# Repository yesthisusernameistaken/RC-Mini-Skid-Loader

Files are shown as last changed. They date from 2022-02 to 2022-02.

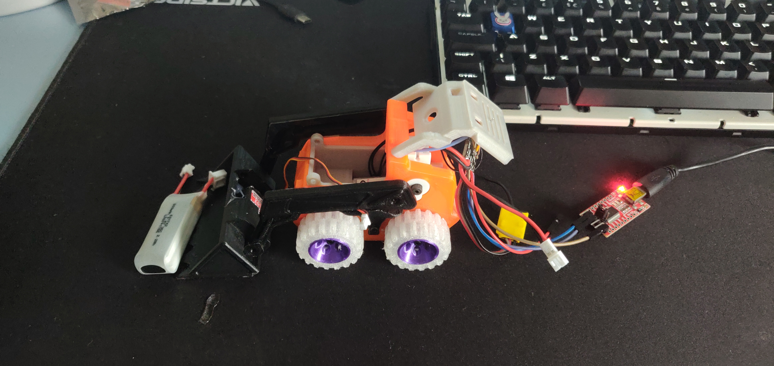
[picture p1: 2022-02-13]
2022-02-13 11.58.56.jpg

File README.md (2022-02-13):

<div align="center">
<h1> RC-Mini-Skid-Loader
</div>

Idea from here: https://blog.naver.com/3dfuns/221406762117
Modified version to use N20 Motors: https://www.thingiverse.com/thing:4548756

Wheels printed in TPU instead of buying Lego versions.

The code on the Tinydrive was not working for some unknown reason. Possibly compatibility issues with the PPM receiver used.
Wrote custom code. Based on code previously used for a project but modified to use the pins and hardware on the Tinydrive.  
Running into an issue where the Servo library disables the pins used for controlling one of the motors. Also might be running out of timers. 

<p align="center">


  ## Shopping List </div>
| Part | Price (€) | Link |
|---|:---:|---|
| TinyDrive | 25 | https://store.flytron.com/collections/electronic-parts/products/tiny-drive-v1-sbus-ppm-1-5a-dual-motor-controller |
| FS-RX2A Pro Receiver | 10 | https://www.aliexpress.com/item/32845028381.html |
| AFRC D1602 Nano 2.2g Mricro Servo | 8 | https://www.banggood.com/AFRC-D1602-Nano-2_2g-Mricro-Servo-Coreless-Digital-Servo-For-RC-Helicopter-Airplane-Car-p-1684246.html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 |
| Wheels 92402 55982 30.4x14mm | 6 | https://www.aliexpress.com/item/32958796717.html? |
| N20 Motors | 10 | https://www.aliexpress.com/item/33022320164.html |
| Type-C Charging Board TP4056 | 1 | https://www.aliexpress.com/item/32649780468.html? |
| 2S Battery | 10 | |
| Total = | 70 | |

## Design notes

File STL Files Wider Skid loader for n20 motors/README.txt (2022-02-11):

Wider 3DFuns Skid loader for n20 motors by 3DFerret on Thingiverse: https://www.thingiverse.com/thing:4548756

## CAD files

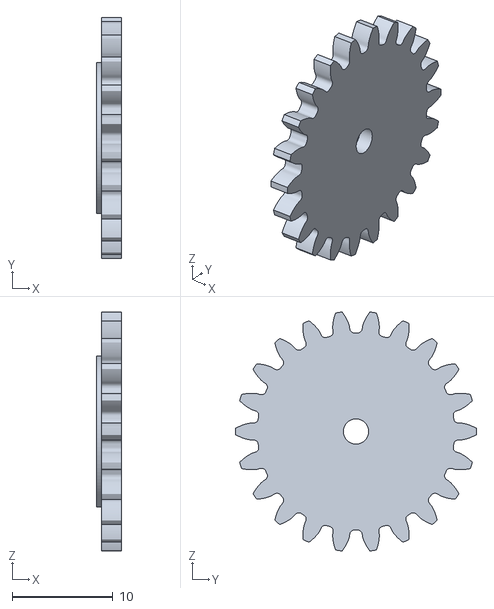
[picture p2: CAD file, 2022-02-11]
STL Files Wider Skid loader for n20 motors/wheel_gear_middle.stl
2.50 x 23.9 x 23.7

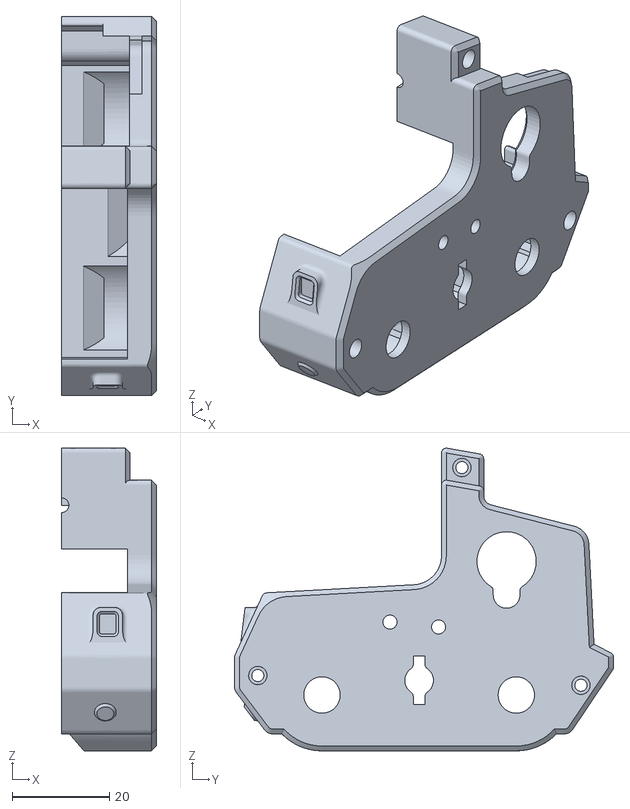
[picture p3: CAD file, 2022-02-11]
STL Files Wider Skid loader for n20 motors/body_right.stl
19.5 x 78.0 x 62.3

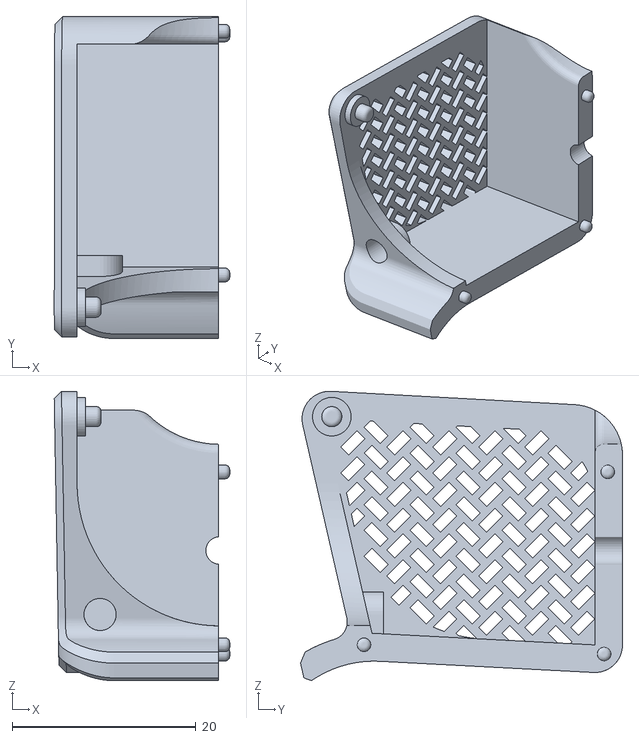
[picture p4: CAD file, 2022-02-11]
STL Files Wider Skid loader for n20 motors/cab_enclosure_right.stl
19.1 x 35.0 x 31.5

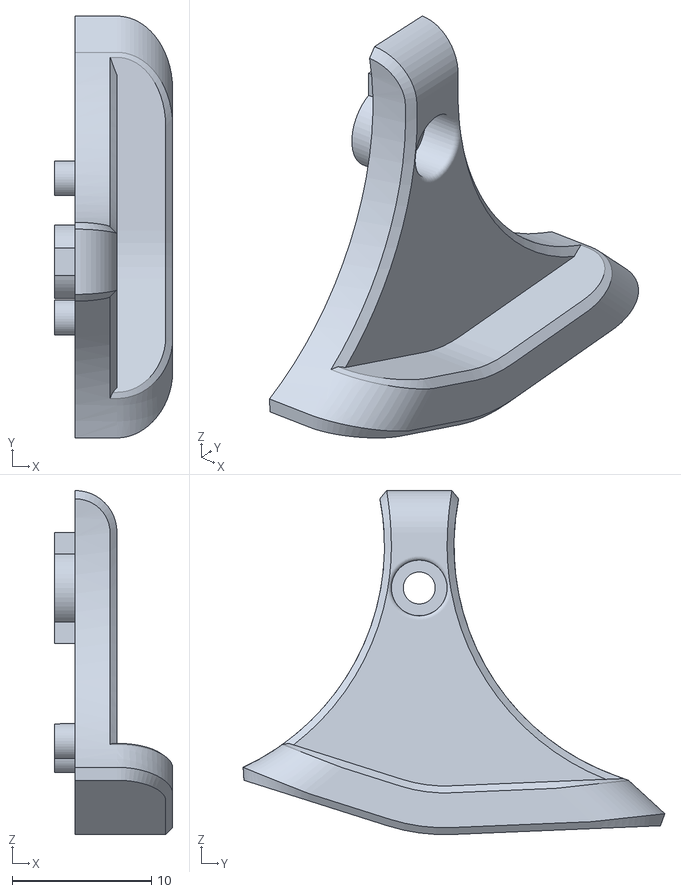
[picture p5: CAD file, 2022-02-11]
STL Files Wider Skid loader for n20 motors/loader_fender_new.stl
8.50 x 30.3 x 24.7

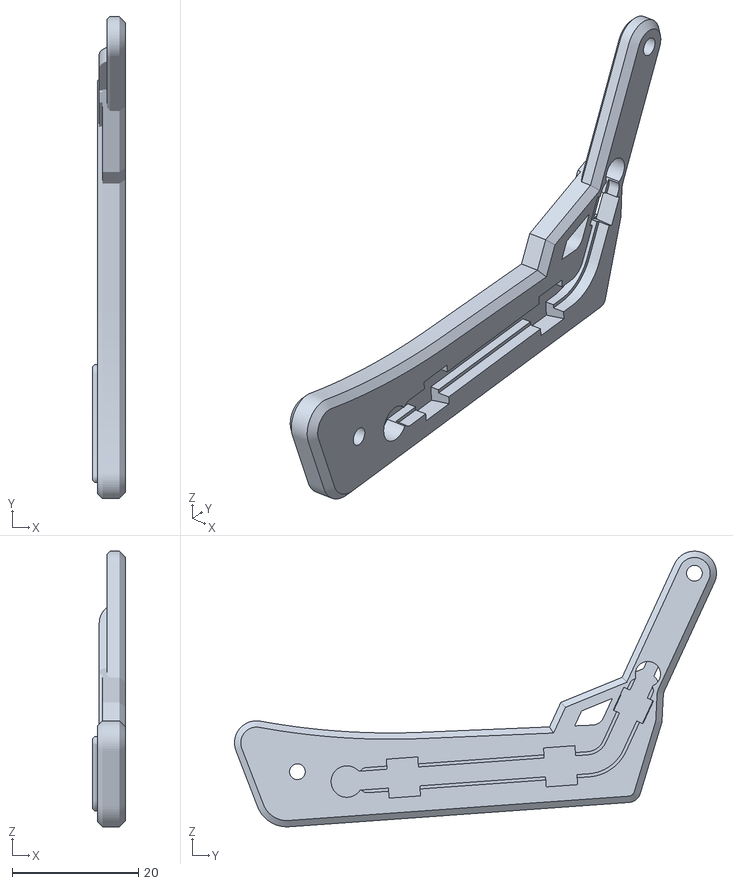
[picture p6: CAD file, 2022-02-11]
STL Files Wider Skid loader for n20 motors/loader_arm_left.stl
5.30 x 76.5 x 43.7

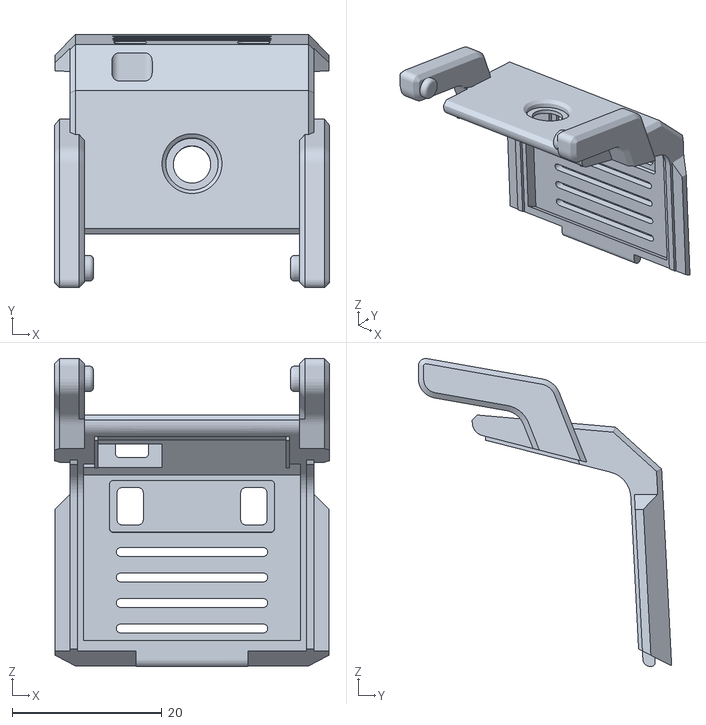
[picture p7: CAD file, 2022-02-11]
STL Files Wider Skid loader for n20 motors/cover_engine.stl
36.7 x 33.8 x 41.1

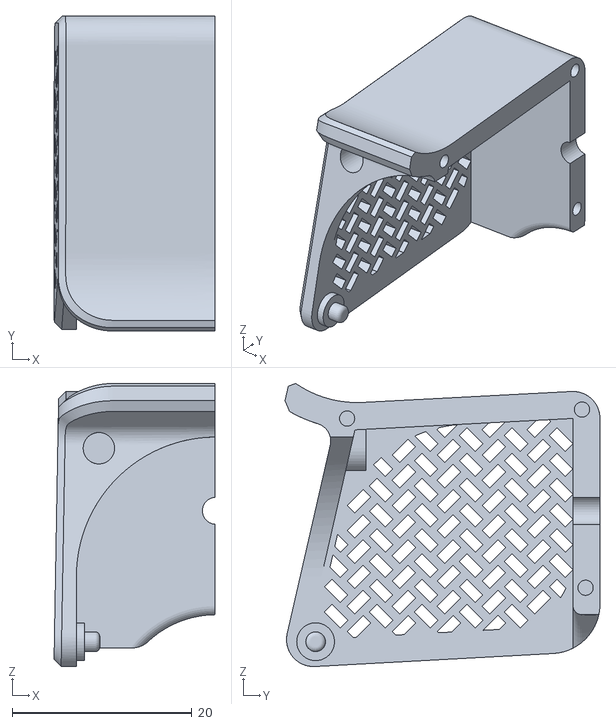
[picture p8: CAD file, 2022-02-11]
STL Files Wider Skid loader for n20 motors/cab_enclosure_left.stl
17.9 x 35.0 x 31.5

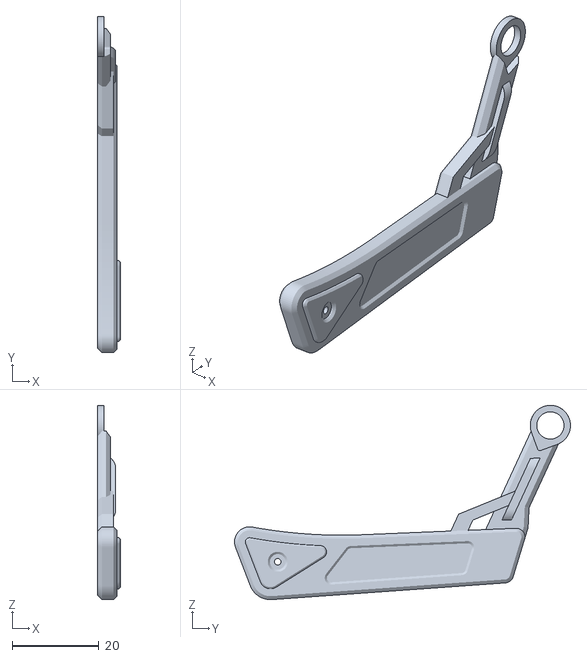
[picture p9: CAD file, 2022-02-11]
STL Files Wider Skid loader for n20 motors/loader_arm_right.stl
5.30 x 77.6 x 44.9

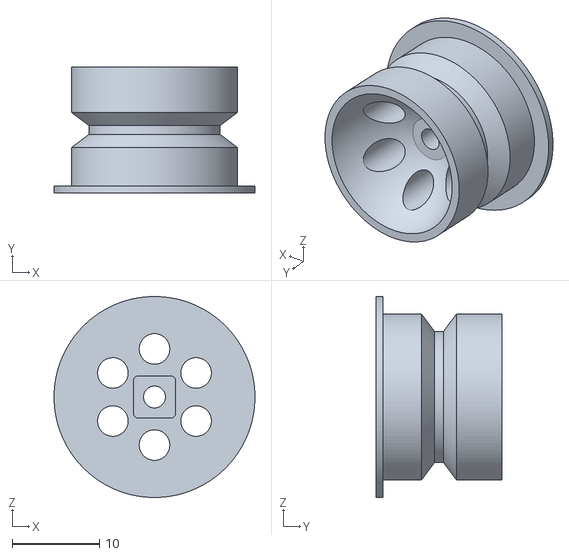
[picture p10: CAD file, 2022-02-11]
STL Files Wider Skid loader for n20 motors/rccar-mn_wheel_30pi.stl
23.0 x 14.4 x 23.0

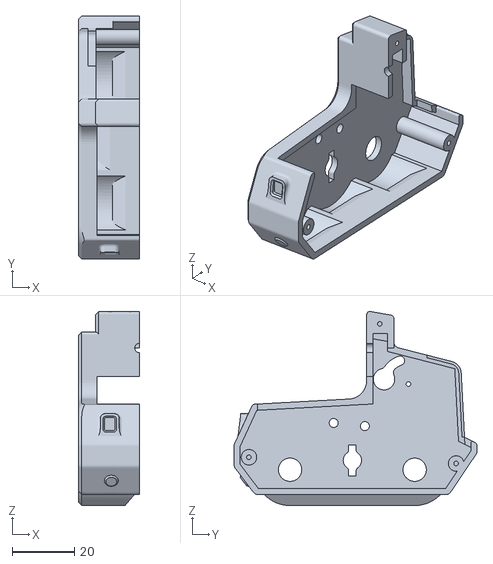
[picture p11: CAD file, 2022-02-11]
STL Files Wider Skid loader for n20 motors/body_left.stl
19.5 x 78.0 x 62.3

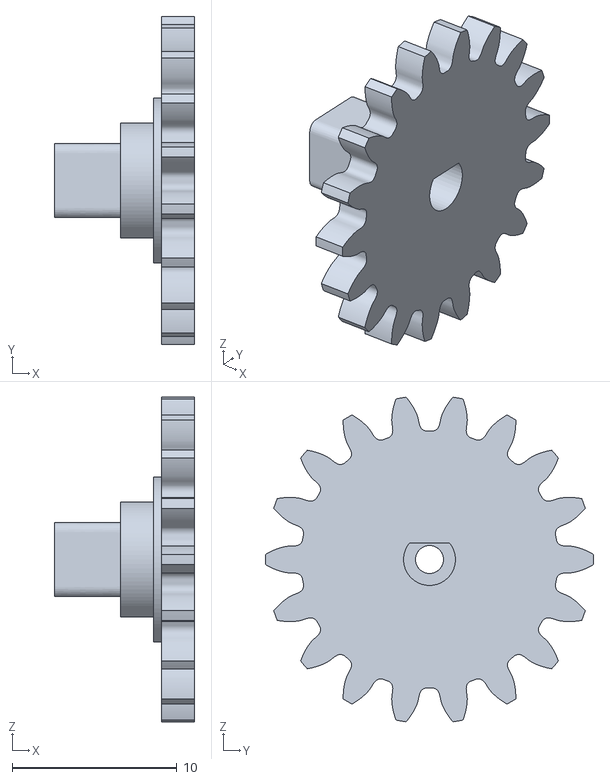
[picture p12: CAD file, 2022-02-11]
STL Files Wider Skid loader for n20 motors/Wheel_gear_slotted_v6.stl
8.50 x 19.9 x 19.7

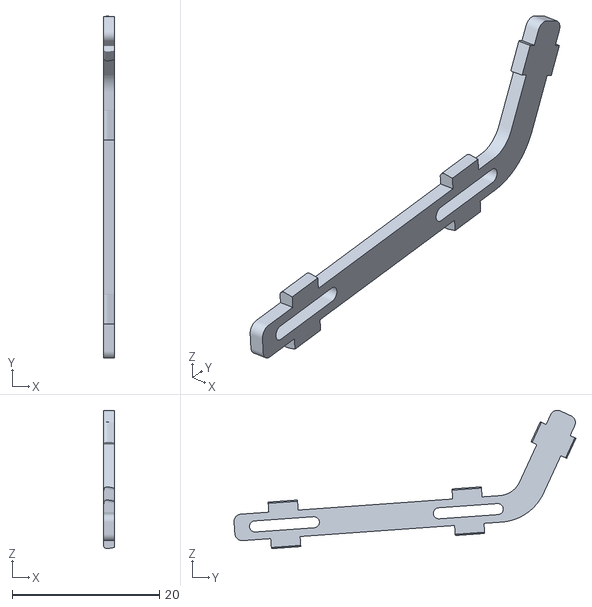
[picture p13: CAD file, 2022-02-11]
STL Files Wider Skid loader for n20 motors/loader_cover_wire_motor.stl
1.50 x 46.4 x 18.8

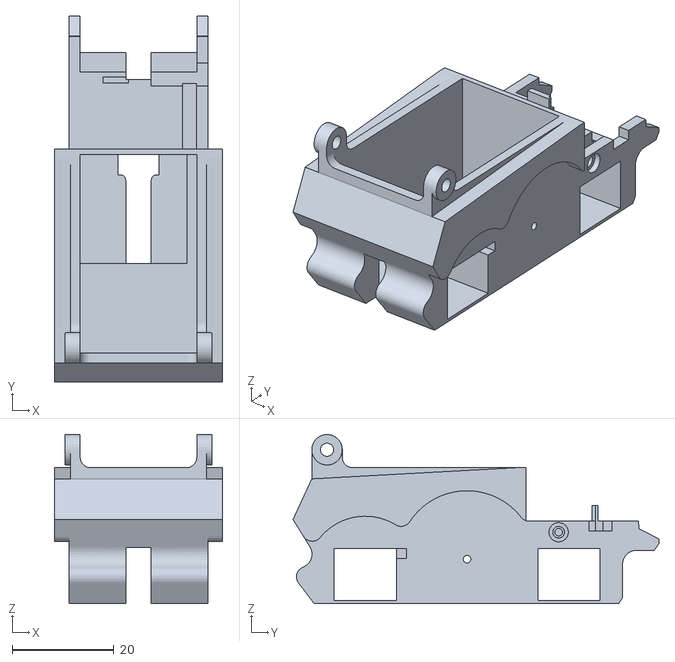
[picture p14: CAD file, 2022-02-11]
STL Files Wider Skid loader for n20 motors/bracket_motor.stl
33.0 x 71.9 x 33.2

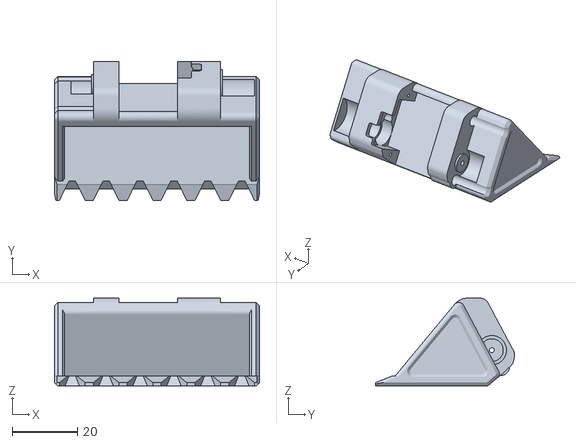
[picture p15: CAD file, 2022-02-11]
STL Files Wider Skid loader for n20 motors/bucket.stl
63.0 x 42.7 x 27.0

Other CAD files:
STL Files Wider Skid loader for n20 motors/loader_fender_new_left.stl
STL Files Wider Skid loader for n20 motors/wheel_gear_dummy.stl
STL Files Wider Skid loader for n20 motors/92402 Lego wheel.stl

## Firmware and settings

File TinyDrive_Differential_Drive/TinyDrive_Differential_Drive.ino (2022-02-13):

#include <PPMReader.h>

/* 
Written by Vincent Y
Alternative code for https://github.com/flytron/TinyDrive
Using RX2A PPM FS-RX2A Pro Receiver Mini RX for Flysky receiver

Flashing the Tinydrive:
Select Tools>Board>Arduino Pro or Pro mini
Processor>ATmega328P (5v, 16Mhz)
-Arduino Firmware Upload Process:
Turn off the TX
Unplug the battery
Press the Upload button of Arduino IDE and wait for compiling
Plug the battery immediately(in 2 seconds) when you see "Uploading..." message on the display
FTDI LEDs will start blinking and you will see "Done Uploading" message in a few seconds.

To do: 
-Change pins to work with the code below
https://github.com/flytron/TinyDrive/blob/main/TinyDrive_v1/TinyDrive_v1.ino
-Add servo support
Can't user servo library as it uses timers and dissables pin 8 and 9
Also causing issues with timer
-Add LED support
-Fix issue with directions not being correct when reversing then turning
-Detect if valid PPM signal or not, stop it from misbehaving when the TX is not on


Done:
-Add reverse 10.02.2022
-Rename motor pins 10.02.2022
-Test out with expected channel set to 8 11.02.2022
This is based on the receiver used and supported PPM
-Add batterty code sensor and test 12.02.2022

*/


//Specific for the Tinydrive
//#define SBUS_ENABLE_PIN A3  // HIGH: Enables the XOR gate to invert the SBUS signal to Standard Serial.  LOW: Standard Serial Input mode. 
#define STATUS_LED 13         // On Board LED pin

// Simplified Status LED Modes 
#define LED_TOGGLE digitalWrite(STATUS_LED,!digitalRead(STATUS_LED));
#define LED_ON digitalWrite(STATUS_LED,HIGH); 
#define LED_OFF digitalWrite(STATUS_LED,LOW);

//Servos
#define SERVO_1 A4          // CH4 Servo PWM signal output.
//#define SERVO_2 A5          // CH5 Servo PWM signal output.
#define HEADLIGHT_PIN 3     // D3(PWM) pin connected to the Base pin of an NPN transistor. [LED+] has a serial 10 Ohm resistor to limit the current. Use AnalogWrite(0-255) to control the light intensity.

//Battery sensor
#define Battery_Sensor_Pin  A6        // Connected to the Battery input over 1/11 voltage divider. 
#define Battery_Sensor_Factor  11.6   // Multiply the reading with this value and you will find the battery voltage in mV  
#define Cell_Min_Voltage 3200         // Minimum 3.2V per cell when the motors off.
uint16_t Battery_Voltage_mV = 0;      // The battery voltage in mV
uint8_t Battery_Cell_Count = 1;       // Detected battery cell count (1 or 2)
#define CHECK_PERIOD 1000L            // Check the battery level in every 1000ms
unsigned long last_check_time = 0L ;  
volatile boolean motors_off = 1;

//Motor stuff
int M1_PHASE = 5;
int M1_DIRECTION = 6;
int M2_DIRECTION = 9;
int M2_PHASE = 8;
int Speed_A = 0;          // Speed of motor
int Speed_B = 0;

// For PPM values, the difference between is the deadband
int lowerLimit = 1420;
int upperLimit = 1520; 

// Initialize a PPMReader on digital pin 2 with 6 expected channels.
// Receiver used JMT RX2A PPM FS-RX2A Pro Receiver Mini RX for Flysky
int interruptPin = 2;
int channelAmount = 6;
PPMReader ppm(interruptPin, channelAmount);



void setup(){

  //Battery setup
  analogReference(INTERNAL);  // Enable internal 1.1v analog reference for the battery voltage readings
  delay(200);                 // Wait 200mS on the startup for the voltage stabilisation. 
  Battery_Voltage_mV =  analogRead(Battery_Sensor_Pin) * Battery_Sensor_Factor; // Read battery voltage in mV
  delay(100);
  // The first read may be faulty due to the ADC referance change on the startup. The next read will be fine.  
  Battery_Voltage_mV =  analogRead(Battery_Sensor_Pin) * Battery_Sensor_Factor; // Read battery voltage in mV
   if (Battery_Voltage_mV>6200)       {
        Battery_Cell_Count = 2;  // Detect 2S liPo if >6.2v
      }else{ 
        Battery_Cell_Count = 1;}  // Run on 1S LiPo mode for 1S LiPo or 3-4x AA Batteries(<=6V) 
  last_check_time = millis (); // set the first battery check time.
      
  //Motor stuff 
  pinMode (M2_DIRECTION, OUTPUT); pinMode (M2_PHASE, OUTPUT); pinMode (M1_PHASE, OUTPUT); pinMode (M1_DIRECTION, OUTPUT);
  pinMode(HEADLIGHT_PIN, OUTPUT); digitalWrite(HEADLIGHT_PIN,LOW);
  
  //The two servos
  pinMode(SERVO_1, OUTPUT); digitalWrite(SERVO_1,LOW);
  //pinMode(SERVO_2, OUTPUT); digitalWrite(SERVO_2,LOW);
  
  //Serial.begin(115200);
  delay(200);
  //march();   // Play The Imperial March 
  pinMode(STATUS_LED, OUTPUT);  // initialize the LED pin as an output.
  LED_ON; 
}

void loop(){
 
  unsigned long PPM_Channel_1 = ppm.latestValidChannelValue(1, 1500);//A
  unsigned long PPM_Channel_2 = ppm.latestValidChannelValue(2, 1500);//E
  unsigned long PPM_Channel_3 = ppm.latestValidChannelValue(3, 1500);//T
  unsigned long PPM_Channel_4 = ppm.latestValidChannelValue(4, 1500);//R
  unsigned long PPM_Channel_5 = ppm.latestValidChannelValue(5, 1500);
  unsigned long PPM_Channel_6 = ppm.latestValidChannelValue(6, 1500);

// Forward. reverse
  if (PPM_Channel_3 > upperLimit) {
    //Stick is pushed upwards, go forward
    Speed_A = map(PPM_Channel_3, upperLimit, 2000, 0, 255);
    Speed_B = Speed_A; 
    digitalWrite(M1_PHASE, LOW); digitalWrite(M2_PHASE, LOW);
  }else if (PPM_Channel_3 < lowerLimit){
    //Stick being pulled down, go backwards
    Speed_A = map(PPM_Channel_3, lowerLimit, 1000, 0, 255);
    Speed_B = Speed_A; 
    digitalWrite(M1_PHASE, HIGH); digitalWrite(M2_PHASE, HIGH);
  }else{
    //Stick in middle position. stop all motors
    Speed_A = 0;
    Speed_B = Speed_A;
  }

  // Steeting 
  if (PPM_Channel_1 < lowerLimit) {
    // Convert the declining X-axis readings from 470 to 0 into increasing 0 to 255 value
    int RMapped = map(PPM_Channel_1, lowerLimit, 1000, 0, 255);
    // Move to left - decrease left motor speed, increase right motor speed
    Speed_A = Speed_A - RMapped;
    Speed_B = Speed_B + RMapped;
    // Confine the range from 0 to 255
    if (Speed_A < 0) {
      Speed_A = 0;    }
    if (Speed_B > 255) {
      Speed_B = 255;    }
  }
  if (PPM_Channel_1 > upperLimit) {
    // Convert the increasing X-axis readings from 550 to 1023 into 0 to 255 value
    int xMapped = map(PPM_Channel_1, 1500, 2000, 0, 255);
    // Move right - decrease right motor speed, increase left motor speed
    Speed_A = Speed_A + xMapped;
    Speed_B = Speed_B - xMapped;
    // Confine the range from 0 to 255
    if (Speed_A > 255) {
      Speed_A = 255;    }
    if (Speed_B < 0) {
      Speed_B = 0;    }
  }

    //Write speed to motors
    analogWrite(M1_DIRECTION, Speed_A);
    analogWrite(M2_DIRECTION, Speed_B);


  digitalWrite(SERVO_1, HIGH);
  delayMicroseconds((PPM_Channel_2/2) + 1000);
  digitalWrite(SERVO_1, LOW);
  





  //Serial.print(String(Speed_A) + " " + String(Speed_B));
  //Serial.println();
  //delay(100); //Wait a bit for motor to speed up







  //Battery check routine
  if ((Speed_A< 10) && (Speed_B < 10)){ //central dead zone
          motors_off = 1;
          //m_throttle = 0;
         // m_direction = 0;        
        }else{
        motors_off = 0;}
       
  // Check for the battery voltage 
   if ((millis() - last_check_time) >= CHECK_PERIOD){
        last_check_time = millis ();
        if (motors_off){ // Measure the battery when the motors off. 
            Battery_Voltage_mV = analogRead(Battery_Sensor_Pin) * Battery_Sensor_Factor; // in mV
            if (Battery_Voltage_mV< (Battery_Cell_Count* Cell_Min_Voltage)) // stop working below the minimum cell voltage and blink the LED. 
               {  while(1){ // Infinite loop 2 short blink 1 second OFF
                  LED_ON
                  delay(100);
                  LED_OFF
                  delay(100);
                  LED_ON
                  delay(100);
                  LED_OFF
                  delay(1000);}
               }
            }   
       }
 
}

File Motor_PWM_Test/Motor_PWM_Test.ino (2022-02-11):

/* 
Varies the speed of two motors from 0 to 100%
Written by Vincent Y
*/


int motora1 = 5;
int motora2 = 6;

int motorb1 = 9;
int motorb2 = 8;

int speeda = 0;    // Speed of motor
int speedb = 0;
 
int speedchange = 5;    // 


void setup(){
  pinMode (motorb1, OUTPUT);
  pinMode (motorb2, OUTPUT);
  pinMode (motora1, OUTPUT);
  pinMode (motora2, OUTPUT);

}
void loop(){
  //In order to change motor direction, change motora1 and motorb2 to high or low
  digitalWrite (motora1, HIGH);
  analogWrite (motora2, speeda);
  analogWrite (motorb1, speeda);
  digitalWrite (motorb2, LOW);

  
  //analogWrite(PWM_A, speeda);           //Both are told to go at the same speed
  //analogWrite(PWM_B, speeda);  
  
   speeda = speeda + speedchange;      //Increase speed
  
  if (speeda == 0 || speeda == 255)     //Once the speed reaches 225 or 0 it changes direction
  {
    speedchange = -speedchange ; 
  }     
     
  delay(100); //Wait a bit for motor to speed up
  
 
}

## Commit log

2022-02-12 Some slight changes
    Just changing code around trying to get the servos working
2022-02-12 Trying to fix jitter issue
    When adding a servo, caused everything to "break". The V2 code in an attempt to test what is causing this.
    [PPM_and_servo_test.ino, TinyDrive_Differential_Drive.ino]
2022-02-13 Trying to solve problem with timer
    [TinyDrive_Differential_Drive.ino]
2022-02-13 Testing out ways to drive the servo without using the servo lib
